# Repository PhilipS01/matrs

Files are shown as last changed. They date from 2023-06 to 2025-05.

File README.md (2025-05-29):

<h1 align="center">MATRS</h1>

<p align="center">



</p>

MATRS (Motion Actuated Turret Remote System) ist ein quelloffenes persönliches Projekt. Ein Miniatur-Geschütz folgt Handbewegungen und feuert auf Kommando.

<p align="center">

</p>

## Hintergrund

Was eigentlich nur ein Wochenend-Projekt zum wiederverwenden einiger Komponenten werden sollte, artete in mein wohl umfangreichstes Mechatronik Projekt aus. Vom Getriebe bis zum Handschuh habe ich so ziemlich alles entworfen, programmiert und fabriziert.

## Features

### Geschoss

MATRS feuert sechs Millimeter Airsoft BBs. Andere Größen könnten jedoch durch einfache Modifizierung am Lauf und Hopper benutzt werden.

### Modi

MATRS hat zwei programmierte Modi, welche mittels Knopfdruck am Handschuh ausgewählt werden können:

#### Stationärer Modus

In diesem Modus rotiert die Turret nicht. Lediglich der Abzug kann betätigt werden, um ein Geschoss abzufeuern.

#### Dynamischer Modus

Hier rotiert die Turret, sodass die Orientierung gleich dem des Handschuhs/Controllers ist (Gieren). Auch die Neigung (Nicken) des Handschuhs wird berücksichtigt.

## Umsetzung

### Gieren

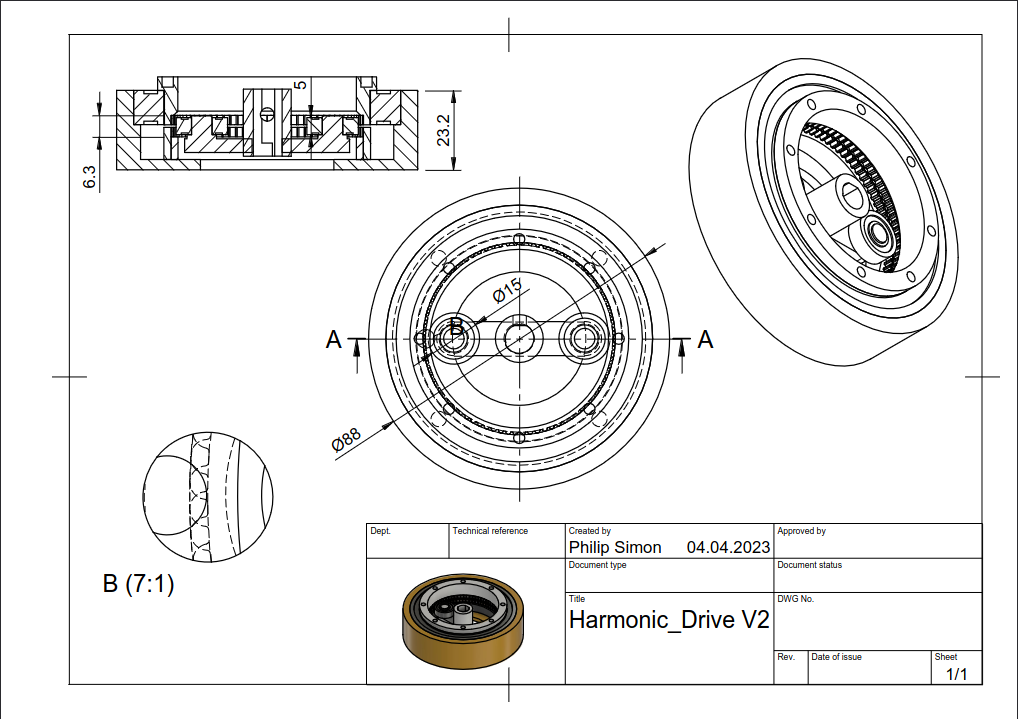
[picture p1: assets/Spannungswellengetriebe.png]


Das Gieren des Geschützes übernimmt ein 39,5:1 **Spannungswellengetriebe**. Als _Flex-Spline_ wurde ein Zahnriemen vom Typ GT2 verwendet, welcher von zwei Kugellagern gespannt wird. Den Antrieb übernimmt in meiner Installation ein Nema 23 Schrittmotor (Closed-Loop), welcher zugegeben etwas überqualifiziert ist.

### Nicken

Das Nicken wird durch ein **Zahnriemengetriebe** mit einem Übersetzungsverhältnis von 3⅓:1 realisiert. Als Antrieb habe ich einen SG90 Mikroservo benutzt. Des weiteren sorgt ein Idler mit einstellbarer Spannung für eine optimale Kraftübersetzung.

### Schießen

Den Schuss-Mechanismus habe ich in dieser Version nicht selbst entworfen. Es handelt sich um eine einfache Airsoft-Gearbox. Der durch die Gearbox freigelassene Luftdruck mündet in dem 3D-gedruckten vorderen Lauf. Die Kugeln werden hierbei von einem Trichter in den Lauf gefüllt.

### Bewegungserfassung

Das **AHRS** (_Attitude Heading Reference System_) wird mittels Sensor-Fusion eines 6-Achsen Beschleunigungssensor und Gyroskops inmitten des Handschuhs umgesetzt. Ein Arduino Nano 33 BLE sorgt für die Beschaffung und Verarbeitung dieser Informationen. Eine **Kalibrierung** und **Homing-Prozedur** direkt nach dem Verbindungsaufbau zwischen Handschuh und Geschütz sorgt für zuverlässige, konstante Nutzung.

### Drahtlose Kommunikation

Des weiteren ist dank des verbauten Chipsets Bluetooth® Low Energy und somit eine kabellose Kommunikation zwischen Controller (Handschuh) und Turret möglich. Die Kalibrierung, das Homing, wie die Auswahl der verschiedenen Modi erfolgt über einen Taster am Handschuh. Zudem erzeugt die Basisstation der Turret Audio-Signale zu bestimmten Ereignissen (wie z.B. beim Wechsel des Modus) und eine LED im Handschuh liefert Einblick in den Zustand der Kommunikation. So bedeutet ein blinkendes Signal bspw. das Daten für die Kalibrierung gesammelt werden.

Es gibt einen **BLE-Service** mit folgenden Charakteristiken:

```cpp
BLECharacteristic headingInt("b3de23b1-12fe-4266-a590-53528c11116d", BLERead, 3);
BLEIntCharacteristic buttonPress("6541935a-5c22-464b-b150-c335eaa92910", BLERead | BLEWrite | BLENotify);
BLEIntCharacteristic triggerPull("626488b2-70d1-4b89-ad13-45e8ee61ebd8", BLERead | BLENotify);
```

Wobei `headingInt` aus drei Byte besteht (platzbedingt, da z.B. 359 (°) > 255):

- Byte 1 und 2 für die Gierungsrichtung
- Byte 3 für das Nicken

Der Nano 33 BLE des Handschuhs macht dabei Gebrauch vom MBED basierten RTOS (_Real Time Operating System_) und implementiert **Multithreading** um die verschiedenen Charakteristiken gleichzeitig aktualisieren zu können.

## Hürden

### AHRS

Ursprüngliche Versuche die Sensor-Daten zu Fusionieren fanden im Zahlenbereich der Quaternionen statt. Letztendlich waren normale Euler-Winkel leichter umzusetzen. Da ein Gimbal-Lock für den Betrieb des Systems irrelevant scheint, ist diese Lösung pragmatischer.

Um Störungen im Input der Sonseren zu reduzieren wird entweder ein simpler Low-Pass Filter angewendet:

```cpp
EulerAngles calcLowPassAngles() {
   EulerAngles angles = calcHeading();

   float pitchf = angles.pitch * 0.25 + (pitchf * (1.0 - 0.25));
   float rollf = angles.roll * 0.25 + (rollf * (1.0 - 0.25));
   float yawf = angles.yaw * 0.25 + (yawf * (1.0 - 0.25));

   return {pitchf, rollf, yawf};
}
```

... oder wie in der derzeitigen Version lediglich die arithmetischen Mittel verwertet:

```cpp
EulerAngles calcAverageAngles() {
   int N = 16;
   float averPitch=0; float averRoll=0; float averYaw=0;
   for (int i=1;i<=N;i++)
   {
      EulerAngles angles = calcHeading();
      averPitch += angles.pitch; averRoll += angles.roll; averYaw += angles.yaw;
   }
   averPitch /= N;    averRoll /= N;  averYaw /= N;

   return {averPitch, averRoll, averYaw};
}
```

### Asynchronizität

Anfangs war für die Kontrolle der Basisstation lediglich ein Arduino Nano 33 BLE vorgesehen. Dieser sollte Kommunikation und Steuerung des Geschützes vornehmen (Gieren & Nicken). Diese Realisierung stellte sich jedoch schnell als unpraktisch heraus. Die Limitierung ergab sich aus der ungenügenden Spannung der digitalen Pins des Nanos für die Steuerung des Schrittmotor-Treibers. Daher wurden die Steuerungsaufgaben auf einen zusätzlichen Arduino Mega umgelegt. Der Arduino Nano der Basisstation übernimmt also lediglich Kommunikationsaufgaben.

Die eingehenden AHRS Daten des Handschuhs übermittelt der Arduino Nano der Basisstation an den Arduino Mega via serieller Schnittstelle.

### Stromversorgung

Die Stromversorgung war das irreführendste Problem. Die Rede ist hierbei von der Stromversorgung der Airsoft Gearbox. Ursprünglich versuchte ich die Stromzufuhr mittels diverser MOSFETs zu switchen. Diese schienen jedoch nie vollständig zu leiten, obwohl die Schwellenspannung lange durch den Arduino MEGA überschritten wurde. Trotz der Spannungs-bestimmten Natur, schienen die MOSFETs aufgrund einer zu geringen Stromstärke geöffnet. Diese Vermutung bestätigte sich nach multiplen Tests mit einer externen Stromversorgung bei gleicher Spannung, aber größerer Stromstärke. Nach vielen Tests entschied ich mich für das Switchen der Gearbox durch ein Relay. Dieses war nun in der Lage verlässlich den benötigten Strom für die Airsoft Gearbox zu schalten.

### Mündungsgeschwindigkeit

Die Schnelligkeit des Projektils ist proportional zum Luftdruck, welcher auf das Projektil wirkt. Jenen Druck gilt es also zu erhöhen, um eine möglichst große Projektilgeschwindigkeit zu verursachen. Um einen konstanten, hohen Druck erzeugen zu können, muss die Toleranz zwischen Kugel/Projektil und Lauf so gering wie möglich sein. Da der Lauf jedoch wie der Rest von MATRS per FDM hergestellt wurde, waren die Ergebnisse sehr volatil. Das Problem konnte größtenteils durch eine nachträgliche Bohrung, sowie Trial-and-Error gelöst werden.

## Weiterführendes

Der ganze Artikel über das Projekt steht auf meiner <a href="https://philipsi.de">Portfolio Website</a> zur Verfügung. In diesem finden Sie neben einer Hardware Liste auch Demonstrationsvideos uvm.!

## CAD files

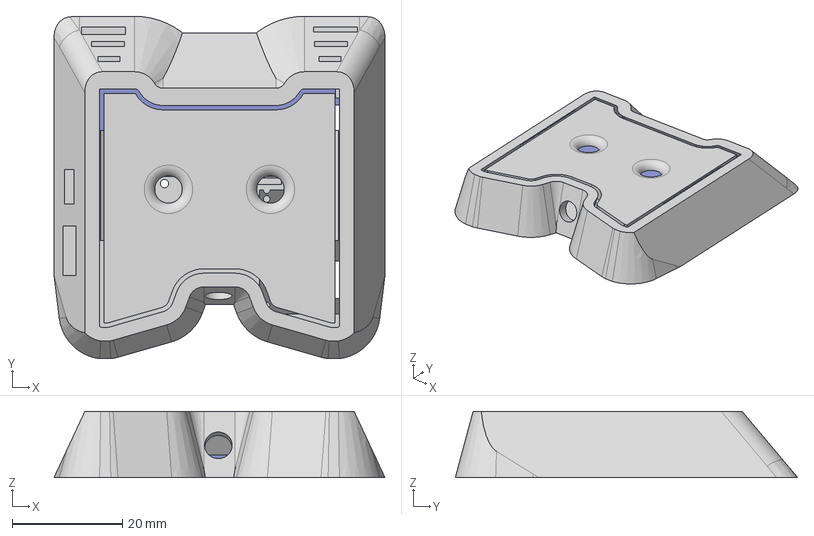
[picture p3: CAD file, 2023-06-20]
3D_models/Glove.step
60.2 x 62.2 x 12.0 mm
Arduino Nano 33 BLE
Lid
StepdDownModule
Case

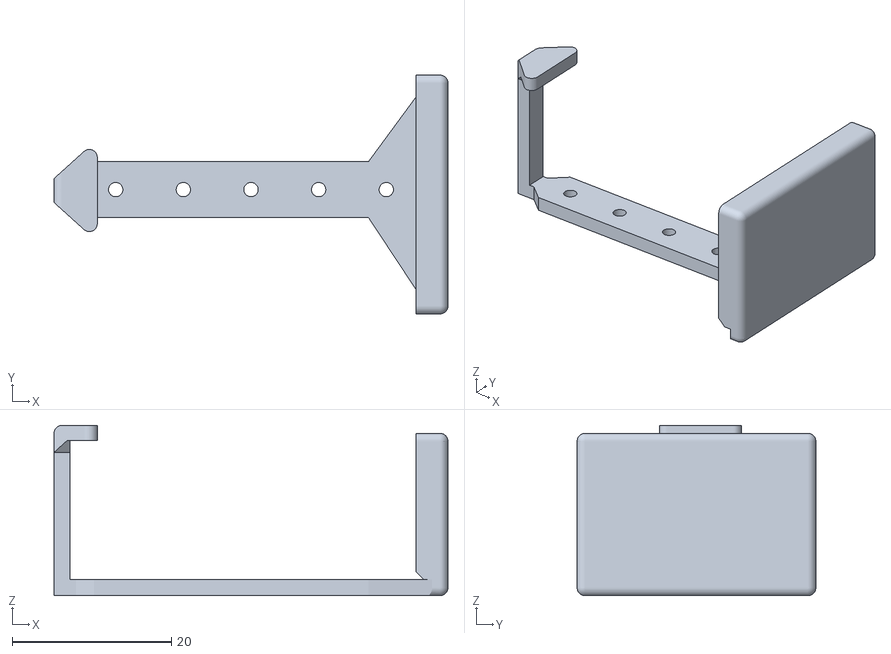
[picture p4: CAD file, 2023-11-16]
STLs/Glove/BatteryPack.stl
49.5 x 30.0 x 21.4

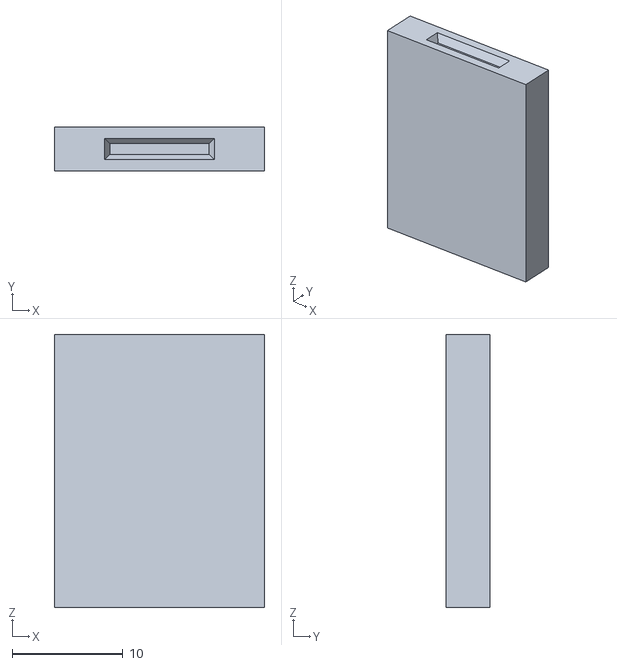
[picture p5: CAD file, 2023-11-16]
STLs/Gun Assembly/Hopper_Lid.stl
19.0 x 4.00 x 24.6

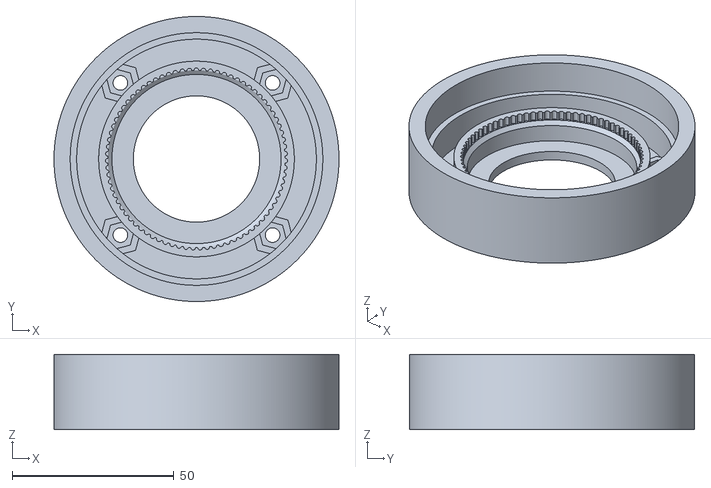
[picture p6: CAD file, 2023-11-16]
STLs/Turret/Case.stl
88.0 x 88.0 x 23.2

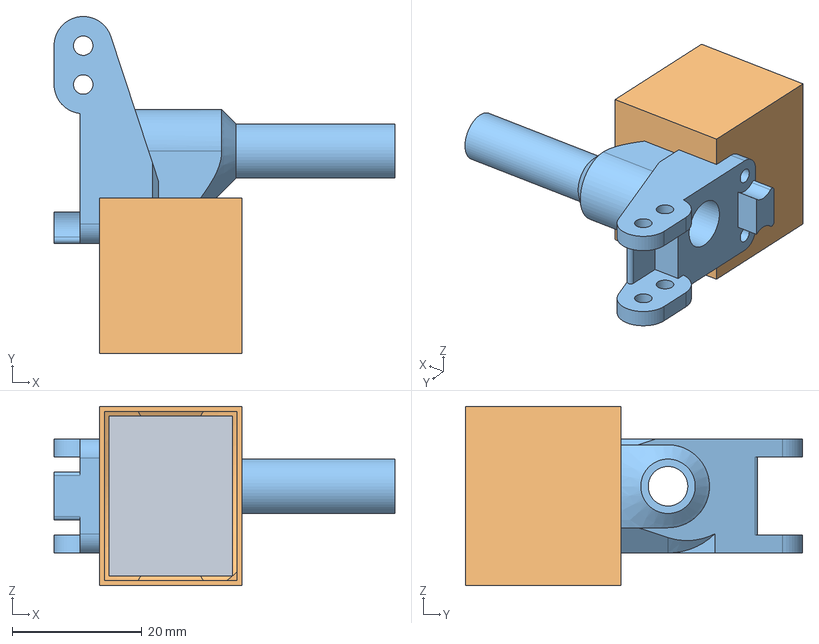
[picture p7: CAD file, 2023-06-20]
3D_models/Gun_Barrel.step
52.6 x 52.0 x 27.6 mm
Lid
Case
Barrel

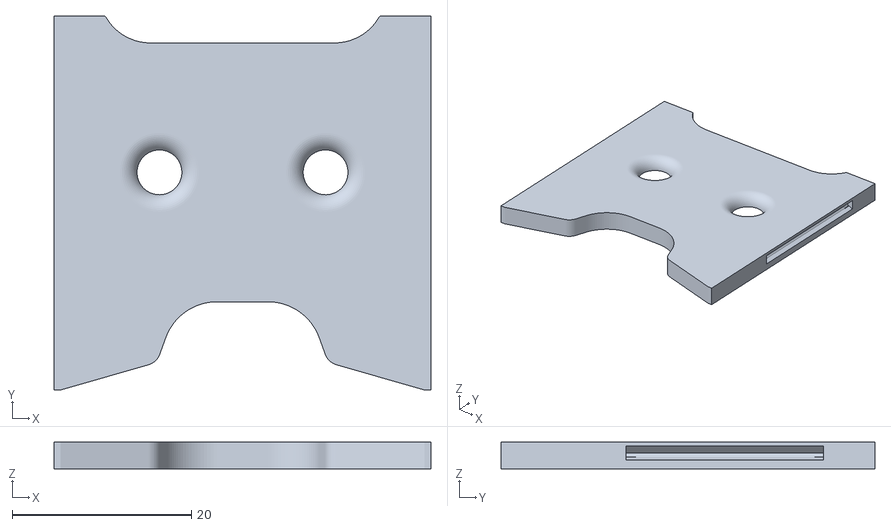
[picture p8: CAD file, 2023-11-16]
STLs/Glove/Lid.stl
42.1 x 41.7 x 3.00

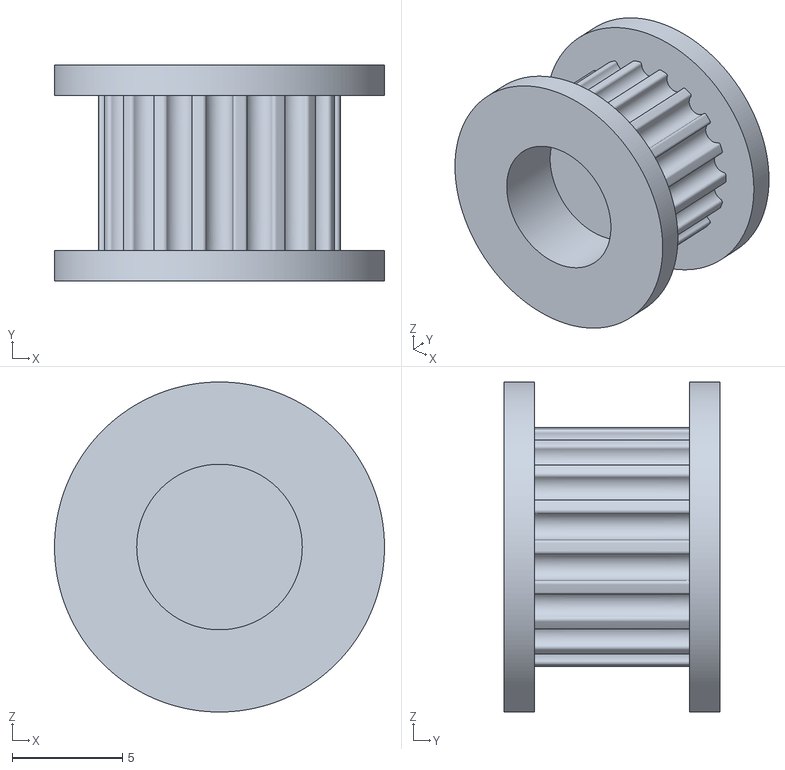
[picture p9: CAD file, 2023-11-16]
STLs/Gun Assembly/Gear1.stl
15.0 x 9.80 x 14.9

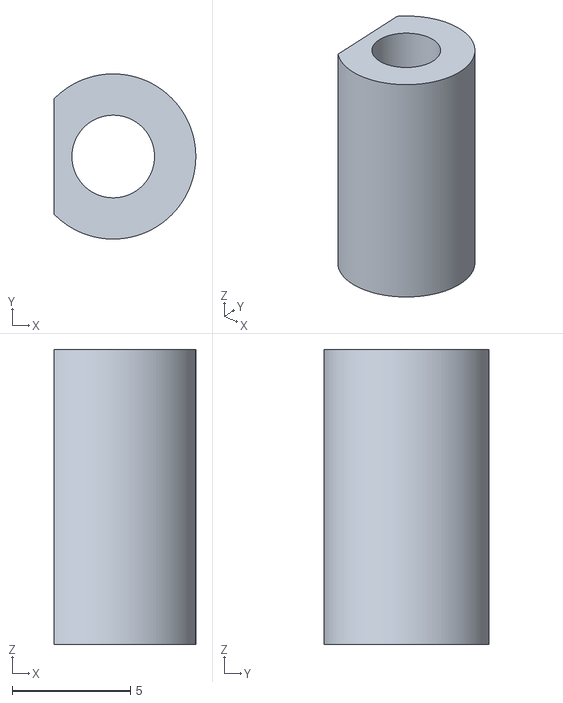
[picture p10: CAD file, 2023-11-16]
STLs/Turret/Base_Standoff_Flat.stl
6.00 x 7.00 x 12.5

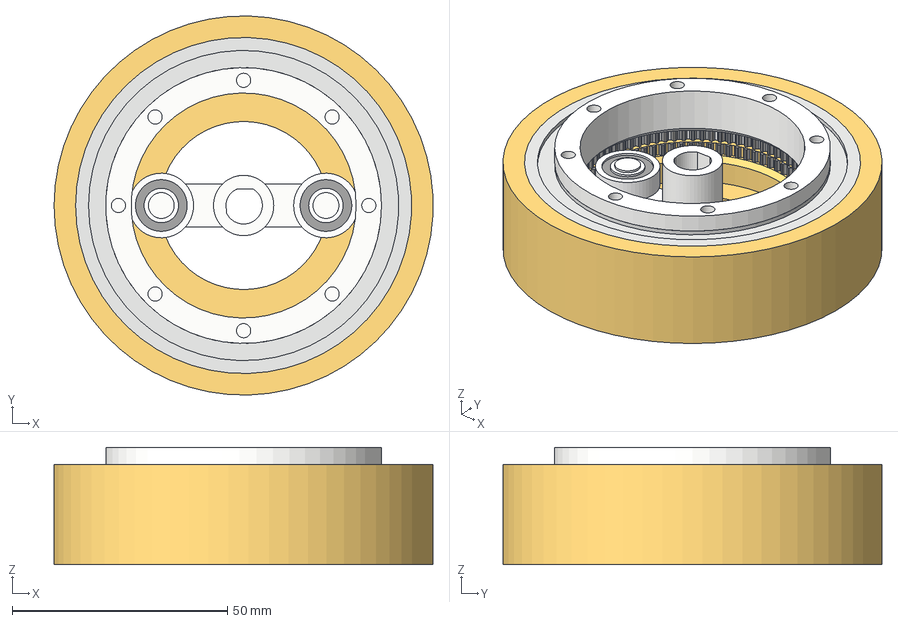
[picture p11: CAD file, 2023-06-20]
3D_models/Harmonic_Drive.step
87.9 x 88.0 x 27.2 mm
Komponente4
6812ZZ Rillenkugellager 60x78x10mm
Wave Generator
696ZZ Kugellager 6x15x5mm x 2
Fixed Circular Spline

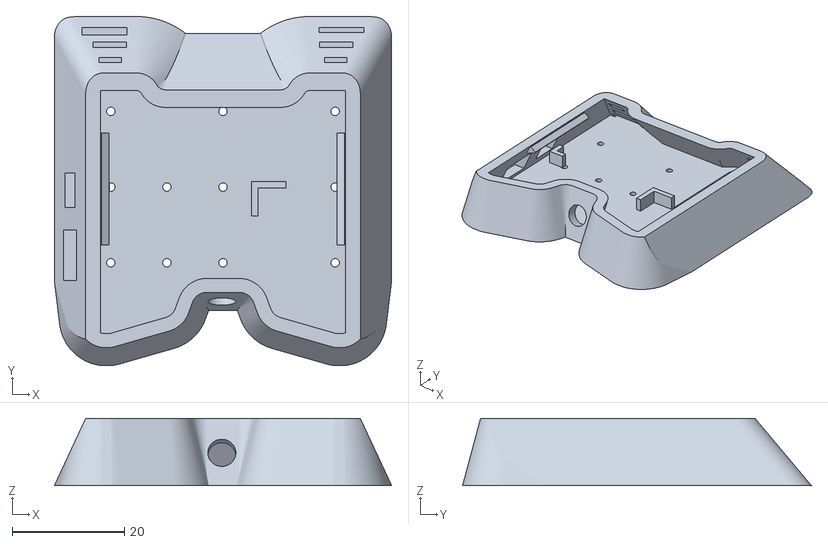
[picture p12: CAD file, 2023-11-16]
STLs/Glove/Case.stl
60.2 x 62.2 x 12.0

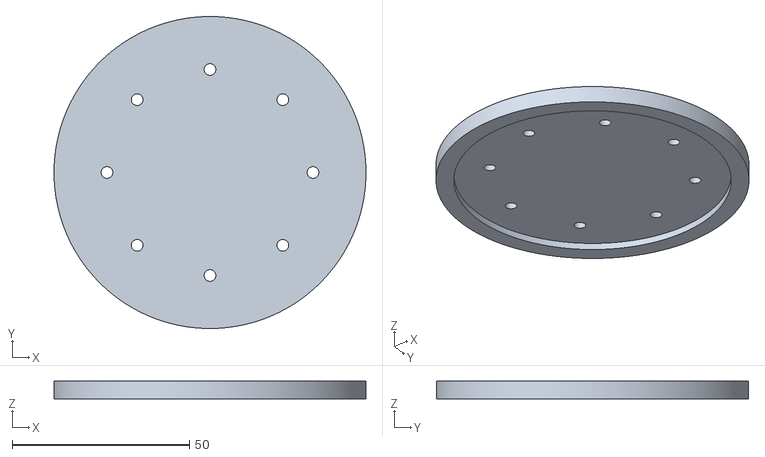
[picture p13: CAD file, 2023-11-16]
STLs/Gun Assembly/Base.stl
88.0 x 88.0 x 5.00

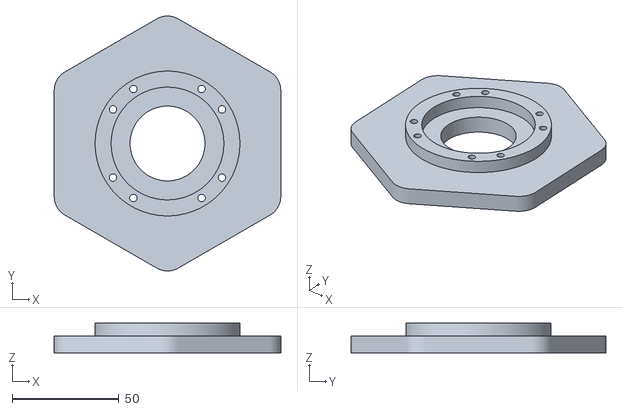
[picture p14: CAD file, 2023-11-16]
STLs/Turret/Base.stl
106.0 x 119.3 x 14.0

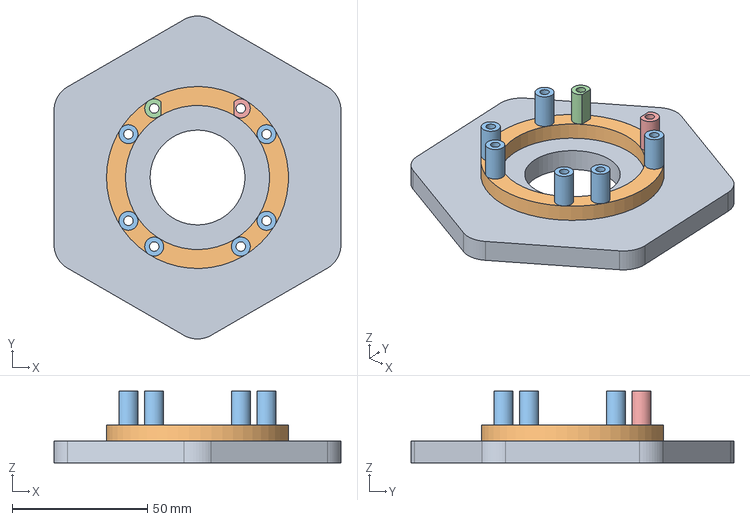
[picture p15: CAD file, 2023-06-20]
3D_models/Base.step
106.0 x 119.3 x 26.5 mm
Base_1
StandOffs

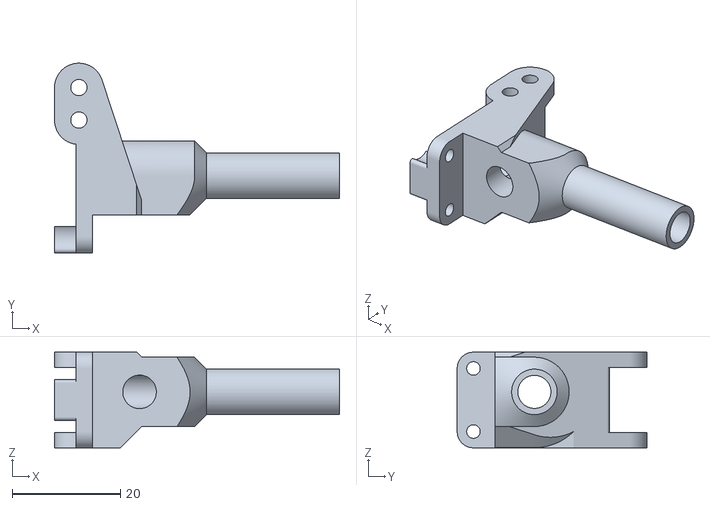
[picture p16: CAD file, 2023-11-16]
STLs/Gun Assembly/GunBarrel.stl
52.6 x 35.0 x 17.6

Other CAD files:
STLs/Turret/Wave Generator.stl
STLs/Gun Assembly/Rod.stl
STLs/Turret/Base_Standoff.stl
STLs/Gun Assembly/MountingPlate.stl
3D_models/Glove.obj
STLs/Gun Assembly/Gear2.stl
STLs/Gun Assembly/Hopper_Case.stl
STLs/Gun Assembly/Idler_Casing.stl
STLs/Turret/Circular Spline.stl

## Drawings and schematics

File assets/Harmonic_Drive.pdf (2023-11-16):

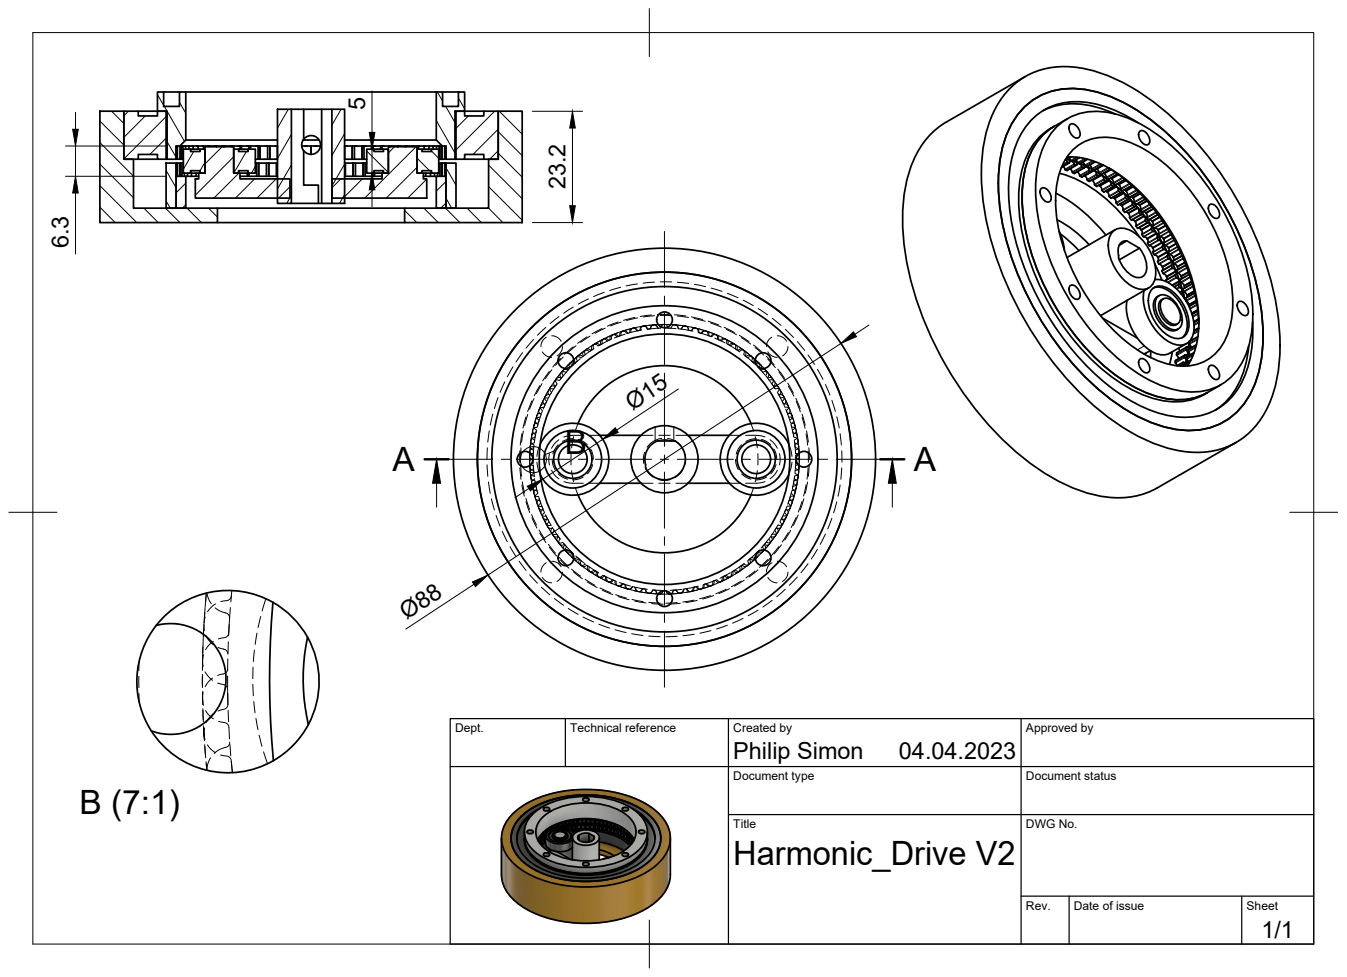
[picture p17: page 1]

Dept. | Technical reference | Created by Philip Simon 04.04.2023 | Approved by

Document type | Document status

Title Harmonic_Drive V2 | DWG No.

Rev. | Date of issue | Sheet 1/1

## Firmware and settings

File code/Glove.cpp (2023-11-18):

#include <Arduino.h>
#include <Arduino_LSM9DS1.h>
#include <ArduinoBLE.h>

#include <mbed.h>
#include <rtos.h>

#define button1 3
#define LED_white 5
const int triggerPin = A5;

volatile bool triggerState = false;

float thetaM;
float phiM;

float thetaG = 0;
float phiG = 0;

float theta;
float phi;
float psi;

float phiRAD;
float thetaRAD;

float magXf = 0;
float magYf = 0;
float magZf = 0;

float pitchf = 0;
float rollf = 0;
float yawf = 0;

float dt;
unsigned long millisOld;

uint32_t heading;
byte heading_and_pitch[3];
float headingRaw;

uint32_t oldheading = 0;

boolean viewInSerialPlotter = true; // true optimises for serial plotter, false for serial monitor

BLEService gloveService("044cddba-fb4d-47a4-90da-9f7578a26931");
BLECharacteristic headingInt("b3de23b1-12fe-4266-a590-53528c11116d", BLERead, 3);

BLEIntCharacteristic buttonPress("6541935a-5c22-464b-b150-c335eaa92910", BLERead | BLEWrite | BLENotify);
BLEIntCharacteristic triggerPull("626488b2-70d1-4b89-ad13-45e8ee61ebd8", BLERead | BLENotify);

bool deviceConnected = false;
bool stationary = false;

// Threads
rtos::Thread thread1;
rtos::Thread thread2;

struct EulerAngles
{
   float pitch;
   float roll;
   float yaw;
};

float EarthMagnetStrength = 49.3; //= µT

boolean magnetOK = false;
uint8_t magnetODRindex = 8; // (0..8)->{0.625,1.25,2.5,5.0,10,20,40,80,400}Hz
uint8_t magnetFSindex = 0;  // 0=±400.0; 1=±800.0; 2=±1200.0 , 3=±1600.0  (µT)

void raw_N_Magnet(unsigned int N, float &averX, float &averY, float &averZ)
{
   float x, y, z;
   averX = 0;
   averY = 0;
   averZ = 0;
   for (int i = 1; i <= N; i++)
   {
      while (!IMU.magnetAvailable())
         ;
      IMU.readRawMagnet(x, y, z);
      averX += x;
      averY += y;
      averZ += z;
      digitalWrite(LED_BUILTIN, (millis() / 125) % 2); // blink onboard led every 250ms
      if ((i % 30) == 0)
         Serial.print('.');
   }
   averX /= N;
   averY /= N;
   averZ /= N;
   digitalWrite(LED_BUILTIN, 0); // led off
}

void calibrateMagnet() // measure Offset and Slope of XYZ
{
   digitalWrite(LED_white, HIGH);
   float x, y, z, Xmin, Xmax, Ymin, Ymax, Zmin, Zmax;
   unsigned long count = 0;
   IMU.setMagnetODR(8);                // Fast rate 400Hz
   raw_N_Magnet(10, Xmin, Ymin, Zmin); // find some starting values
   Xmax = Xmin;
   Ymax = Ymin;
   Zmax = Zmin;
   int i = 0;
   while (digitalRead(button1) == HIGH) // measure until enter key pressed
   {
      raw_N_Magnet(10, x, y, z); // average over a number of samples to reduce the effect of outlyers
      Xmax = max(Xmax, x);
      Xmin = min(Xmin, x);
      Ymax = max(Ymax, y);
      Ymin = min(Ymin, y);
      Zmax = max(Zmax, z);
      Zmin = min(Zmin, z);
      i++;
   }

   // signal that calibration is done
   digitalWrite(LED_white, LOW);
   delay(300);
   digitalWrite(LED_white, HIGH);
   delay(300);
   digitalWrite(LED_white, LOW);

   IMU.setMagnetOffset((Xmax + Xmin) / 2, (Ymax + Ymin) / 2, (Zmax + Zmin) / 2);                                                                        // store offset
   IMU.setMagnetSlope((2 * EarthMagnetStrength) / (Xmax - Xmin), (2 * EarthMagnetStrength) / (Ymax - Ymin), (2 * EarthMagnetStrength) / (Zmax - Zmin)); // store slope
   magnetOK = true;
   IMU.setMagnetODR(magnetODRindex);
}

void magnetometerDoNMeasurements(unsigned int N, float &averX, float &averY, float &averZ)
{
   float x, y, z;
   averX = 0;
   averY = 0;
   averZ = 0;
   for (int i = 1; i <= N; i++)
   {
      while (!IMU.magnetAvailable())
         ;
      IMU.readMagnet(x, y, z);
      averX += x;
      averY += y;
      averZ += z;
   }
   averX /= N;
   averY /= N;
   averZ /= N;
}

void accelerometerDoNMeasurements(unsigned int N, float &averX, float &averY, float &averZ)
{
   float x, y, z;
   averX = 0;
   averY = 0;
   averZ = 0;
   for (int i = 1; i <= N; i++)
   {
      while (!IMU.accelAvailable())
         ;
      IMU.readAccel(x, y, z);
      averX += x;
      averY += y;
      averZ += z;
   }
   averX /= N;
   averY /= N;
   averZ /= N;
}

void gyroscopeDoNMeasurements(unsigned int N, float &averX, float &averY, float &averZ)
{
   float x, y, z;
   averX = 0;
   averY = 0;
   averZ = 0;
   for (int i = 1; i <= N; i++)
   {
      while (!IMU.gyroAvailable())
         ;
      IMU.readGyro(x, y, z);
      averX += x;
      averY += y;
      averZ += z;
   }
   averX /= N;
   averY /= N;
   averZ /= N;
}

EulerAngles calcHeading()
{

   float magX, magY, magZ;
   float accX, accY, accZ;
   float gyrX, gyrY, gyrZ;

   // average measurements to reduce a little noise

   magnetometerDoNMeasurements(5, magX, magY, magZ);
   accelerometerDoNMeasurements(5, accX, accY, accZ);
   gyroscopeDoNMeasurements(5, gyrX, gyrY, gyrZ);

   thetaM = atan2(accX / 9.81, accZ / 9.81) / 2 / 3.141592654 * 360;
   phiM = atan2(accY / 9.81, accZ / 9.81) / 2 / 3.141592654 * 360;

   dt = (millis() - millisOld) / 10000.;
   millisOld = millis();

   // complimentary filter for pitch (theta) and roll (phi)
   theta = (theta + gyrY * dt) * .90 + (thetaM * .10);
   phi = (phi - gyrX * dt) * .90 + (phiM * .10);

   IMU.readMagnet(magX, magY, magZ);

   phiRAD = phi / 360 * (2 * PI);
   thetaRAD = theta / 360 * (2 * PI);

   float Xm;
   float Ym;

   // low pass filter for magnetometer
   magXf = magX * 0.25 + (magXf * (1.0 - 0.25));
   magYf = magY * 0.25 + (magYf * (1.0 - 0.25));
   magZf = magZ * 0.25 + (magZf * (1.0 - 0.25));

   // tilt compensated vector calculations for heading
   Xm = magXf * cos(thetaRAD) + magZf * sin(thetaRAD);
   Ym = magXf * sin(phiRAD) * sin(thetaRAD) + magYf * cos(phiRAD) - magZf * sin(phiRAD) * cos(thetaRAD);

   // Xm=magX*cos(thetaRAD)-magY*sin(phiRAD)*sin(thetaRAD)+magZ*cos(phiRAD)*sin(thetaRAD);
   // Ym=magY*cos(phiRAD)+magZ*sin(phiRAD);

   // final heading angle calculation
   psi = atan2(Ym, Xm) / (2 * PI) * 360;

   if (psi < 0)
   {
      psi = 360 + psi;
   }

   // raw heading
   headingRaw = atan2(magX, magY) / (2 * 3.14) * 360;

   // Gyro data filtered
   // thetaG=thetaG+gyrY*dt;
   // phiG=phiG-gyrX*dt;

   EulerAngles angles;

   angles.pitch = theta;
   angles.roll = phi;
   angles.yaw = psi;

   return angles;
}

EulerAngles calcAverageAngles()
{
   int N = 16;
   float averPitch = 0;
   float averRoll = 0;
   float averYaw = 0;
   for (int i = 1; i <= N; i++)
   {
      EulerAngles angles = calcHeading();
      averPitch += angles.pitch;
      averRoll += angles.roll;
      averYaw += angles.yaw;
   }
   averPitch /= N;
   averRoll /= N;
   averYaw /= N;

   return {averPitch, averRoll, averYaw};
}

EulerAngles calcLowPassAngles()
{
   EulerAngles angles = calcHeading();

   float pitchf = angles.pitch * 0.25 + (pitchf * (1.0 - 0.25));
   float rollf = angles.roll * 0.25 + (rollf * (1.0 - 0.25));
   float yawf = angles.yaw * 0.25 + (yawf * (1.0 - 0.25));

   return {pitchf, rollf, yawf};
}

bool triggered = true;
void triggerCallback()
{
   while (true)
   {
      if (analogRead(triggerPin) > 390 && triggered)
      {
         triggerPull.writeValue((uint32_t)0);
         digitalWrite(LED_white, LOW);
         triggered = false;
      }
      else if (analogRead(triggerPin) <= 390)
      {
         triggerPull.writeValue((uint32_t)1);
         digitalWrite(LED_white, HIGH);
         triggered = true;
      }
      rtos::ThisThread::yield();
   }
}

void headingCallback()
{
   while (true)
   {
      if (stationary == false)
      {
         EulerAngles angles = calcAverageAngles(); // calculate heading
         heading = angles.yaw;

         // only update when tilted if there was a significant change in heading
         if (angles.pitch > 15 && (sqrt((oldheading - heading) * (oldheading - heading))) > 8)
         {
            Serial.print("Heading is at ");
            Serial.print(heading);
            Serial.println(" degrees");

            if (heading > 255)
            {
               heading_and_pitch[0] = (uint32_t)255;
               heading_and_pitch[1] = heading - (uint32_t)255;
            }
            else
            {
               heading_and_pitch[0] = heading;
               heading_and_pitch[1] = 0;
            }
            heading_and_pitch[2] = angles.roll; // roll is pitch bc of rotation in glove mounting

            headingInt.writeValue(heading_and_pitch, 3); // and update the heading characteristic
            oldheading = heading;
         }
         // when not very tilted just update normally
         if (angles.pitch < 15)
         {
            if ((sqrt((oldheading - heading) * (oldheading - heading))) > 3)
               Serial.print("Heading is at ");
            Serial.print(heading);
            Serial.println(" degrees");

            if (heading > 255)
            {
               heading_and_pitch[0] = (uint32_t)255;
               heading_and_pitch[1] = heading - (uint32_t)255;
            }
            else
            {
               heading_and_pitch[0] = heading;
               heading_and_pitch[1] = 0;
            }
            heading_and_pitch[2] = angles.roll; // roll is pitch bc of rotation in glove mounting

            headingInt.writeValue(heading_and_pitch, 3); // and update the heading characteristic
            oldheading = heading;
         }
      }
      rtos::ThisThread::yield();
   }
}

void setup()
{
   Serial.begin(9600);
   // while(!Serial);                   // wait till the serial monitor connects

   pinMode(button1, INPUT_PULLUP);
   pinMode(LED_white, OUTPUT);

   delay(1);
   if (!IMU.begin())
   { // initialize the magnetometer
      Serial.println("Failed to initialize IMU!");
      while (1)
         ;
   }

   /*****************   For a proper functioning of the compass the magnetometer needs to be calibrated    ********************
   *****************   Replace the lines below by the output of the DIY_Calibration_Magnetometer sketch   ********************/

   // Calibrate Magnetometer
   calibrateMagnet();

   // Accelerometer code
   IMU.setAccelFS(3);
   IMU.setAccelODR(5);
   IMU.setAccelOffset(-0.015487, -0.010553, -0.001073);
   IMU.setAccelSlope(0.997558, 0.993326, 1.003259);

   // Gyroscope code
   IMU.setGyroFS(2);
   IMU.setGyroODR(5);
   IMU.setGyroOffset(1.581726, -0.599609, 0.703522);
   IMU.setGyroSlope(1.797827, 1.807842, 1.948031);

   /******************************************************************************************************************************
   ****  FS  Full Scale        range (0=±400 | 1=±800 | 2=±1200 | 3=±1600  (µT)                                              *****
   ****  ODR Output Data Rate  range (6,7,8)=(40,80,400)Hz | not available on all chips (0..5): (0.625,1.25,2.5,5.0,10,20)Hz *****
   *******************************************************************************************************************************/

   IMU.magnetUnit = MICROTESLA; //   GAUSS   MICROTESLA   NANOTESLA

   if (!BLE.begin())
   {
      Serial.println("* Starting Bluetooth Low Energy module failed!");
      while (1)
         ;
   }

   BLE.setLocalName("TurretGlove");
   BLE.setAdvertisedService(gloveService);      // add the service UUID
   gloveService.addCharacteristic(headingInt);  // add the heading characteristic
   gloveService.addCharacteristic(buttonPress); // add the button characteristic
   gloveService.addCharacteristic(triggerPull); // add the trigger characteristic

   BLE.addService(gloveService); // Add the heading service
   byte oldh[3] = {0, 0, 0};
   headingInt.writeValue(oldh, 3); // set initial value for this characteristic
   triggerPull.writeValue((uint32_t)0);

   BLE.advertise();
   Serial.println("Arduino Nano 33 BLE Sense (Central Device). Waiting for connections...");

   thread1.start(headingCallback);
   thread2.start(triggerCallback);

   millisOld = millis();
}

bool pressed = true;
void loop()
{
   // wait for a Bluetooth® Low Energy central
   BLEDevice central = BLE.central();

   // if a central is connected to the peripheral:
   if (central)
   {
      Serial.print("Connected to central: ");
      // print the central's BT address:
      Serial.println(central.address());
      // turn on the LED to indicate the connection:
      digitalWrite(LED_BUILTIN, HIGH);

      // check the heading level every 500ms while the central is connected:
      while (true)
      {
         if (central.connected())
         {

            // BUTTONS
            if (digitalRead(button1) == LOW)
            { // pressed
               buttonPress.writeValue((uint32_t)1);
               // wait for confirmation --> stationary mode activated or not
               uint32_t value;
               delay(1500);
               // buttonPress.readValue(value);
               // if (value == 0)
               stationary = !stationary;
               pressed = true;
            }
            else if (digitalRead(button1) == HIGH && pressed)
            {
               buttonPress.writeValue((uint32_t)0);
               digitalWrite(LED_BUILTIN, HIGH);
               pressed = false;
            }

            // controller.run();
            rtos::ThisThread::yield();
         }
      }

      // when the central disconnects, turn off the LED:
      digitalWrite(LED_BUILTIN, LOW);
      Serial.print("Disconnected from central: ");
      Serial.println(central.address());
      stationary = false;
      pressed = true;
   }
}

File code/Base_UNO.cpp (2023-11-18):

#include <AccelStepper.h>
#include <time.h>
#include <Wire.h>
#include <Servo.h>

// Pins
#define dirPin 2
#define stepPin 3
#define enablePin 4
#define servoPin 9

// Misc
#define motorInterfaceType 1
#define maxSpeed 10000

#define gearRatio 39.5
#define stepsPerRevolution 2048.

#define servo_gearRatio 3.333;

uint32_t heading;

uint32_t pitch;
float pitch_float;
int pitch_offset = 8;

AccelStepper stepper = AccelStepper(motorInterfaceType, stepPin, dirPin);
Servo pitchServo;

void receiveEvent(int bytes)
{
  heading = 0;
  // read the 2 bytes (because heading can be > 255)
  for (int i = 0; i < 2; i++)
  {
    heading += Wire.read();
  }
  pitch = Wire.read();
  pitch_float = (pitch + pitch_offset) * servo_gearRatio;
}

void rotate()
{
}

void setup()
{
  Wire.begin(9);
  Wire.onReceive(receiveEvent);

  Serial.begin(9600);

  pinMode(enablePin, OUTPUT);
  digitalWrite(enablePin, LOW); // enable stepper

  stepper.setMaxSpeed(maxSpeed);

  stepper.setAcceleration(maxSpeed);
  stepper.setSpeed(maxSpeed);

  stepper.setCurrentPosition(0); // set current pos to home (0 steps)

  pitchServo.attach(servoPin);
}

void loop()
{
  int currentHeading = map(stepper.currentPosition(), 0, (stepsPerRevolution * gearRatio), 0, 360);
  int delta_angle = heading - currentHeading;
  if (delta_angle > 180)
  {
    delta_angle = (360 - delta_angle) * -1;
    // stepper.setSpeed(abs(maxSpeed) * -1);
  }
  else if (delta_angle < -180)
  {
    delta_angle = 360 - abs(delta_angle);
    // stepper.setSpeed(maxSpeed);
  }

  // Serial.println(delta_angle);
  stepper.move(delta_angle);
  while (stepper.distanceToGo() != 0)
  {
    if (delta_angle < 0)
    {
      stepper.setSpeed(maxSpeed * -1);
    }
    else
    {
      stepper.setSpeed(maxSpeed);
    }
    stepper.runSpeed();
  }

  if (pitch < 90)
  {
    pitchServo.write(pitch_float);
  }
}

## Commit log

2023-11-16 added main project files
    [Base.step, Base.stl, Base_Standoff.stl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]
2023-11-17 readme and tree structure
    [Base.stl, Base_Standoff.stl, Base_Standoff_Flat.stl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]

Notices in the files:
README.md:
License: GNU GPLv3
